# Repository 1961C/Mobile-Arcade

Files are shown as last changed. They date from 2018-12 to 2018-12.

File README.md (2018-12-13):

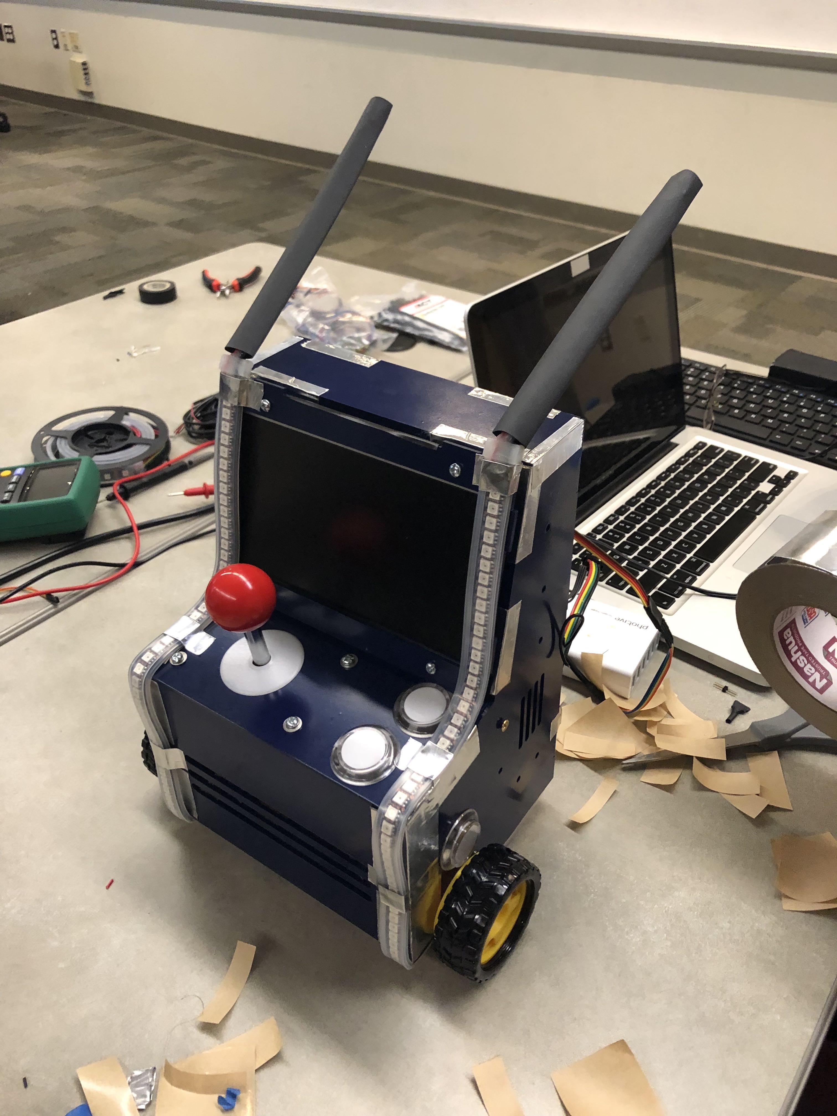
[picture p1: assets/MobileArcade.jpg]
Mobile Arcade


### Table of Contents
* [Concept](#concept)
* [System Design](#system-design)
  * [Physical Enclosure](#physical-enclosure)
  * [Arcade Emulator](#arcade-emulator)
  * [Low-level Control](#low-level-control)
    * [Drive System](#drive-system)
    * [Lighting](#lighting)
  * [Power](#power)
* [Instructions](#instructions)
* [Results](#results)
* [Improvements](#improvements)

## Concept

> "Develop a mobile arcade cabinet that can be controlled over Bluetooth to enable ultimate portability and usability, while maintaining retro charm."

The Mobile Arcade was designed to incorporate a retro gaming experience with a quirky mobile chassis. The original idea was centered around a table top arcade experience with additional entertainment features, including vibrant and responsive lighting. In order to better suit and entertain the target audience (children aged 9 through 14), mobility was incorporated as well. With this in mind, the following design requirements were set:
1. Fully functional, single player, arcade system (ability to play NES and Atari games)
2. Visually pleasing enclosure with a retro feel
3. Interactive lighting
4. Basic Bluetooth-controlled mobility

## System Design

The design of the mobile arcade was divided into distinct subsystems: the physical enclosure, the arcade emulator, the low-level drive system and lighting control. Each of these systems are outlined here.

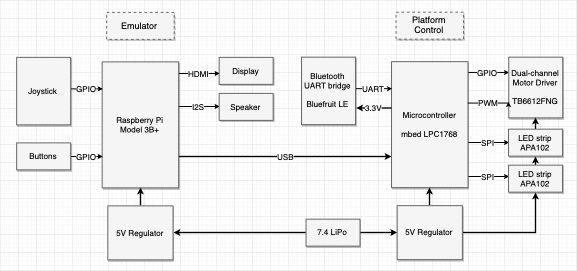
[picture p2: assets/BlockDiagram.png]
Block Diagram


* Raspberry Pi: Main processor
  * Handles arcade game emulator and UI
  * Interfaces with joystick and buttons
* Mbed LPC1768: Secondary processor
  * Handles lighting (LED strips)
  * Handles drive system (remotely commanded via the Bluetooth bridge)
* Dual-channel Motor Driver: Controls 2 motors in a tank-drive configuration
* Power: Li-Po battery and 5V regulator supply power to all components

### Physical Enclosure

The enclosure was designed using Dassault Systems’ Solid Works. Each portion of the seven component design was fitted together in software to ensure accurate dimensioning. The enclosure was then fabricated using 3/32" clear acrylic sheets and laser-cut at the Invention Studio.

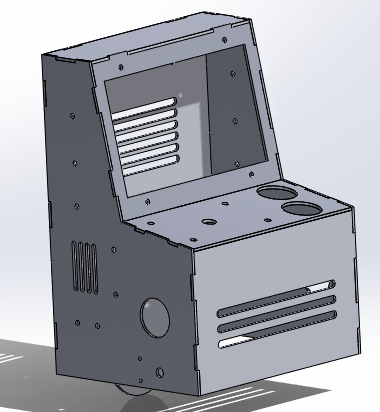
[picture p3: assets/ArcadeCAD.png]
CAD design


The overall shape of the enclosure resembles that of a standard arcade cabinet, with a few notable exceptions. The design is much simpler than standard cabinets, reducing the number of distinct components that need to be fabricated. Additionally, the cabinet incorporates mounting holes near the front specifically designed to accommodate geared drive motors. Along with the rear-mounted skid, this produces a "tank drive" configuration which allows the enclosure to maneuver deftly around its environment.

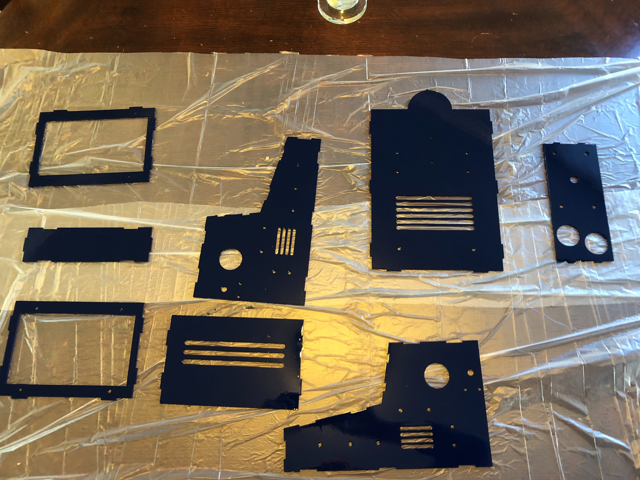
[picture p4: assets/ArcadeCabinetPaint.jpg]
Before cabinet assembly


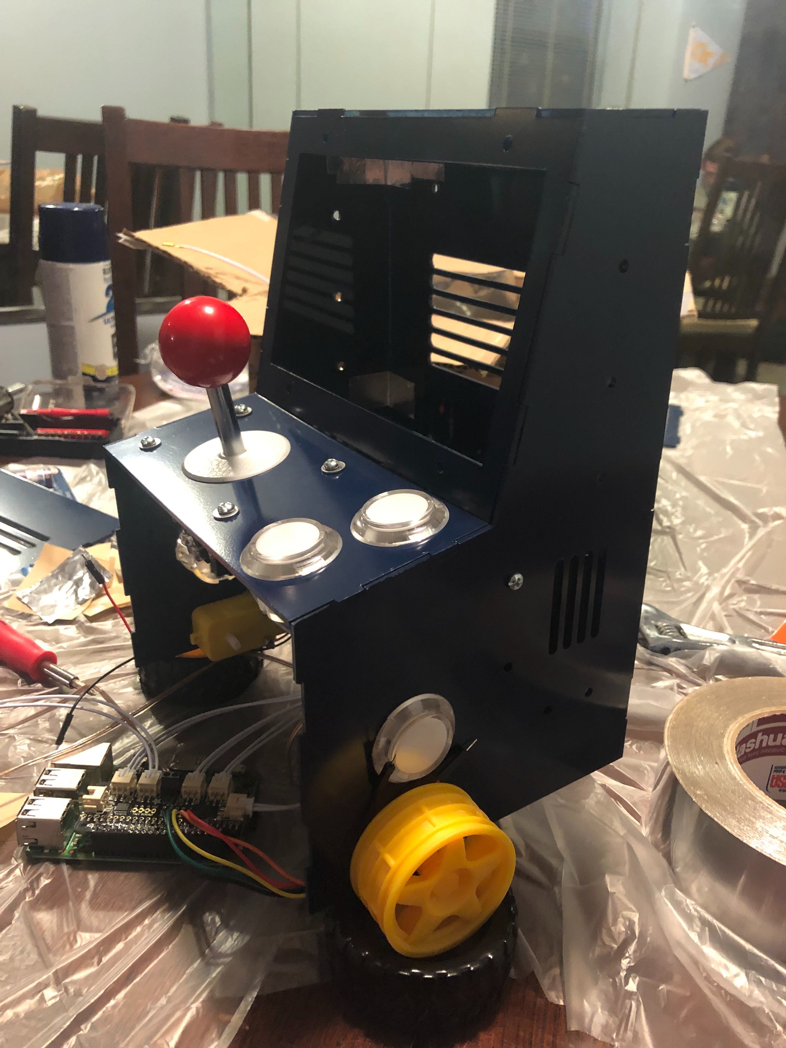
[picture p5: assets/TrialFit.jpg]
Trial fit

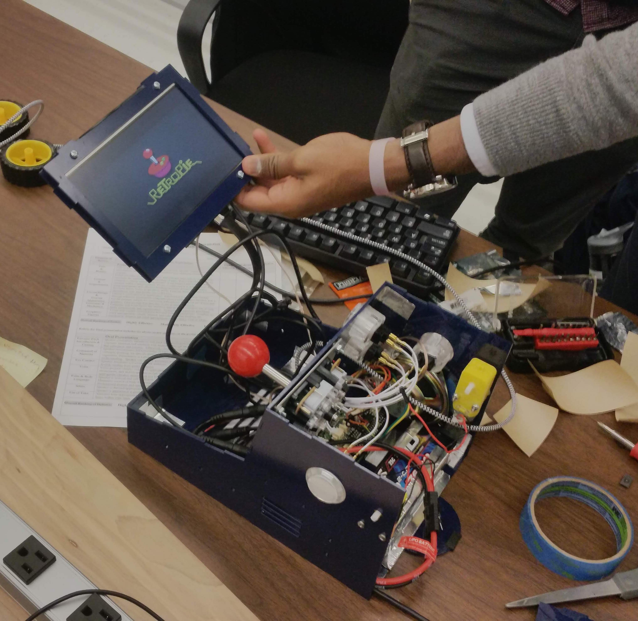
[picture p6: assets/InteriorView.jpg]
Interior view


Holes to fit the arcade controls (joystick and buttons) and LCD screen were included. Details about each of these is covered in the next section.

### Arcade Emulator

The emulation portion of the mobile arcade was split into two portions: the physical controls and the emulation software. The raspberry pi acts as the emulation computer for this project. A small LCD screen is used and is mounted above the joystick. This LCD uses hdmi to connect to the pi.

#### _Arcade Controls_

For controlling the arcade, a standard arcade joystick configuration with four additional buttons was chosen. The following parts were acquired from Adafruit to accomplish this:

* [Joystick](https://www.adafruit.com/product/480)
* [Button](https://www.adafruit.com/product/471)
* [Control Bonnet](https://www.adafruit.com/product/3422)
* [Connection Wires](https://www.adafruit.com/product/1949)
* [Speaker](https://www.adafruit.com/product/1314)

The joystick and buttons each have a specific location they fit into within the enclosure, and were chosen before the CAD model was finalized. The control bonnet connects directly to the GPIO header on the raspberry pi and allows each of the other elements to easily interface with the emulation software. 

Once each physical element is installed, [this guide](https://learn.adafruit.com/adafruit-arcade-bonnet-for-raspberry-pi) outlines the process of formally installing the Control Bonnet on the pi. In order for it to function correctly, specific software needs to be installed on the pi. This should be done after the emulation software is installed, as outlined below.

#### _Emulation Software_

The common emulation software [RetroPie](https://retropie.org.uk/) was chosen for this project. Retropie works seamlessly with the raspberry pi, the primary processor on the mobile arcade, and offers decent functionality. Installation is made fairly easy by the fact that the Retropie foundation provides a disk image for the raspberry pi. The steps that were followed for installing the software are as follows:

1. Download the Retropie disk image from their website
2. Burn the image to the raspberry pi's SD card
3. Boot the system and connect it to the ethernet using wifi or ethernet
4. Install the Control Bonnet software (Refer to previous section)
5. Follow the automatic key-bindings dialog
6. Copy ROM files to the appropriate location

Further details about this process (excluding the Control Bonnet) can be found on the [RetroPie](https://retropie.org.uk/) website.

### Low-level Control

The Mbed microcontroller was used to implement low-level lighting and drive system control. In order to neatly connect the Mbed to the Bluetooth bridge, motor driver, and the LED strips, a single-layer PCB was designed in Eagle and fabricated at the Mechanical Engineering electronics lab. 90º headers were used so that the connections occupied minimal vertical space.

The Eagle files for the PCB can be found [here](https://github.com/1961C/Mobile-Arcade/tree/master/eagle).

Mbed code can be found [here](https://os.mbed.com/users/abraha2d/code/MobileArcade/).

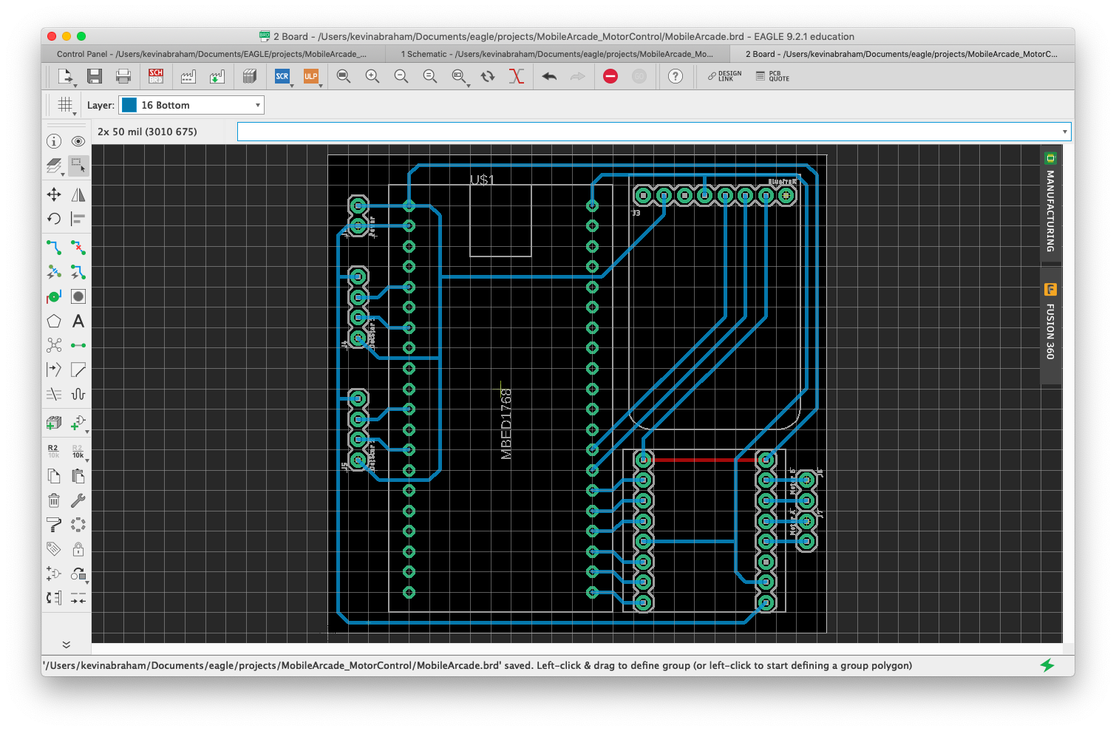
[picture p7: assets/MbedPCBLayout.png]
Mbed PCB design


#### Drive System

The drive system consists of two motors in a tank-drive configuration, with a rear skid for stability. Wheels were added to both sides of the motors (2 visible outside, 2 hidden inside). Not only does this improve stability and ensure traction, it also adds a level of redundancy to the drive system.

A custom Mbed library was used to control the motor driver. The basic library (located [here](https://os.mbed.com/users/simon/code/Motor/)) was extended to add a short brake feature. The extended motor driver library can be found [here](https://os.mbed.com/users/abraha2d/code/Motor/).

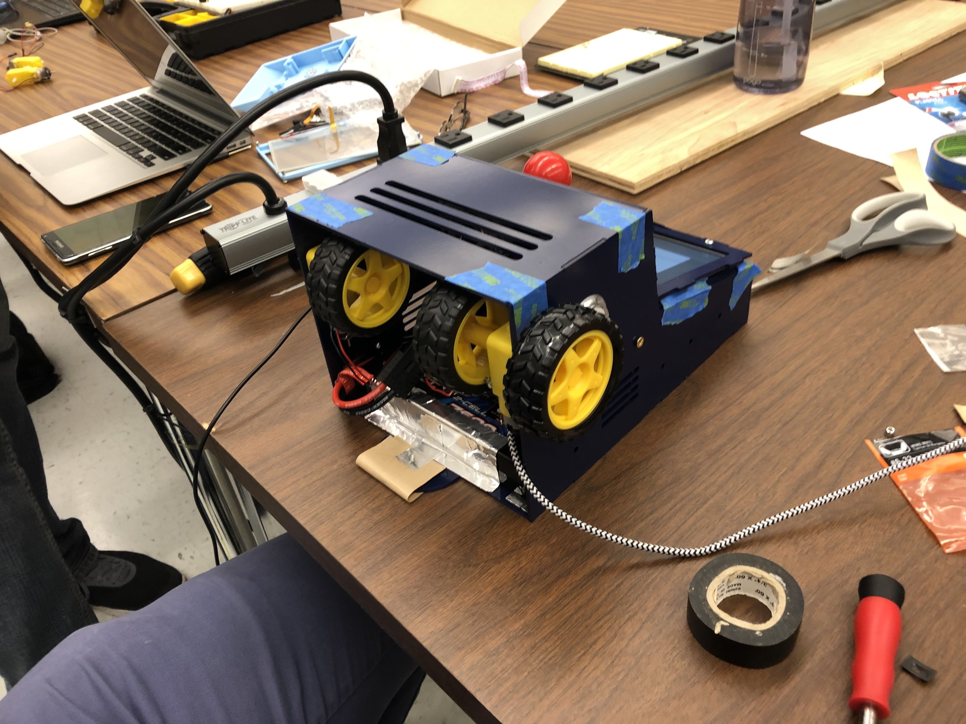
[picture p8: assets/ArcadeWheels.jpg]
Wheel setup


#### Lighting

[Dotstar LED strips](https://www.adafruit.com/product/2239) were used to implement the interactive lighting features of the Mobile Arcade. These were chosen over NeoPixels due to the standard SPI interface and relaxed timing requirements of the integrated APA102 chip, allowing for relatively easy interface with the Mbed. Since no official library was available for interfacing with the APA102, a simple library was created that fulfilled our needs (available [here](https://os.mbed.com/users/abraha2d/code/APA102/)).

The Mbed controls the LED strips in a way that simulates the actions of a real-world vehicle. Simulated lighting effects include headlights, foglights, blinkers, tail/brake lights, reverse lights, and underglow. These lighting effects are controlled in an appropriate way in relation to the movement of the enclosure.

The Mbed also accepts input from the Raspberry Pi over USB serial to synchronize lighting effects to certain events in the arcade emulator. For example, on emulation startup, a startup animation is shown on the LEDs. Other effects include a similar shutdown animation, as well as lighting theme changes when games are started/stopped.

### Power

The Mobile Arcade is powered using a wiring harness connected to a large lithium-ion battery pack. A 5V 3A regulator, connected the harness, is used to provide power for the Raspberry Pi, Mbed LPC1768, motors, and LED strips. The LCD is able to plug directly into the harness without further regulation. Fuses are integrated into the harness to protect sensitive components.

## Instructions

### Hardware setup

* Wiring harness
  * Battery power flows into a two way splitter
    * LCD Screen is powered off of one
    * 5V Regulator connects to the other
  * The 5V Regulator poweres the following items
    * Raspberry pi using a modified Micro USB Cable
    * MBed by powering its custom PCB Directly
    * Motors and LED scrips through the PCB
* Mbed PCB wiring
  * Connect 5V regulator output to power input
  * Connect DotStar LED strips to LED strip outputs
  * Connect motor leads to motor outputs
  * Insert Mbed, Bluetooth bridge, and motor driver in appropriate slots
  * Connect Mbed to Raspberry Pi with a USB cable
* Raspberry Pi Arcade Bonnet wiring ([Guide](https://learn.adafruit.com/adafruit-arcade-bonnet-for-raspberry-pi/connections))
  * Attach each button to one of the wire harness JST connector leads
  * Connect all buttons and the joystick to the Adafruit control bonnet
  * Using speaker wire, attach the speaker to the speaker header on the control bonnet

### Mbed setup

* Upload Mbed code (located [here](https://os.mbed.com/users/abraha2d/code/MobileArcade/))

### Raspberry Pi setup

* Follow RetroPie setup (located [here](retropie.org.uk))
  * Install Adafrit bonnet support software (located [here](https://learn.adafruit.com/adafruit-arcade-bonnet-for-raspberry-pi/software))
* Add runcommand scripts
  * Details about the runcommand scripts can be found [here](https://github.com/RetroPie/RetroPie-Setup/wiki/runcommand#runcommand-onstart-and-runcommand-onend-scripts)
  * Copy the files from '/runcommnads' in this repository to '/opt/retropie/configs/all/' on the raspberry pi
  * Plug the MBED into the pi using USB and ensure that the port (/dev/ttyXXXX) is correct in both runcommand files

## Results

[Demo](https://youtu.be/UGc3tqysLSs)

## Improvements

* Better connection between RPi and mBed
* Intgrate additional 5V regulator
* Add a caster to the back of the enclosure

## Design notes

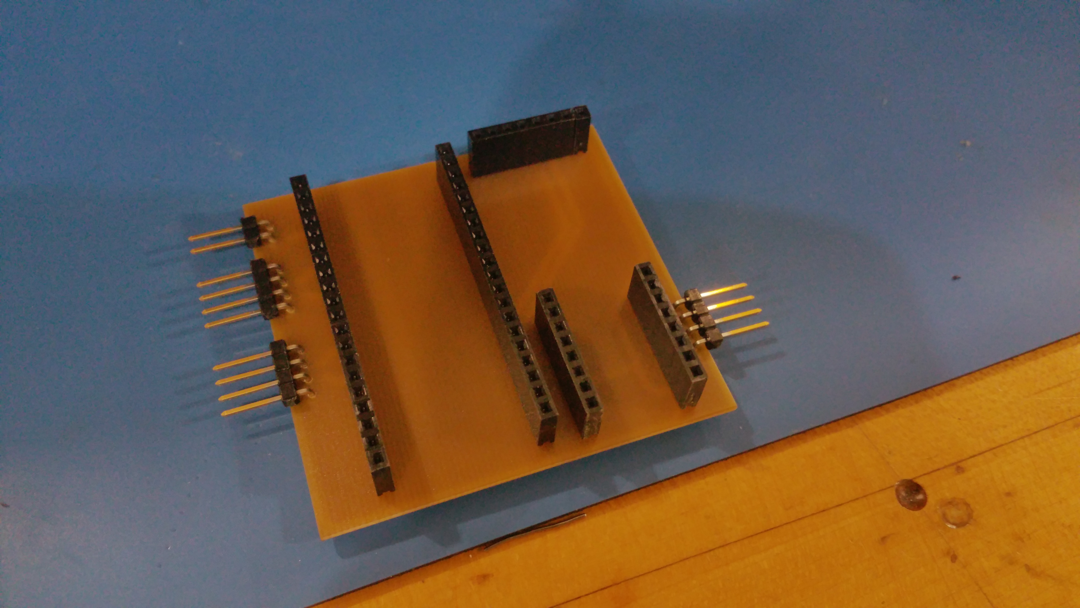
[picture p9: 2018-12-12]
assets/MbedPCB.jpg

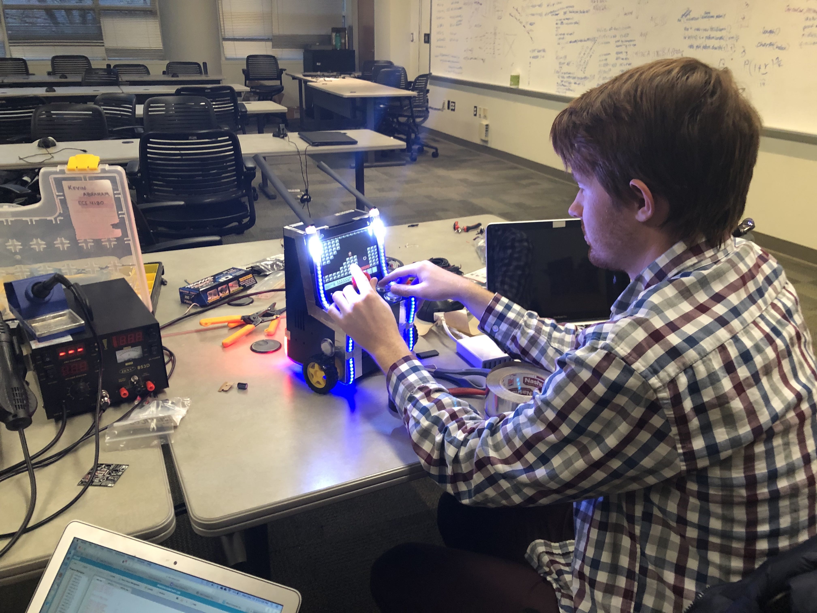
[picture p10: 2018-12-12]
assets/Demo.jpg

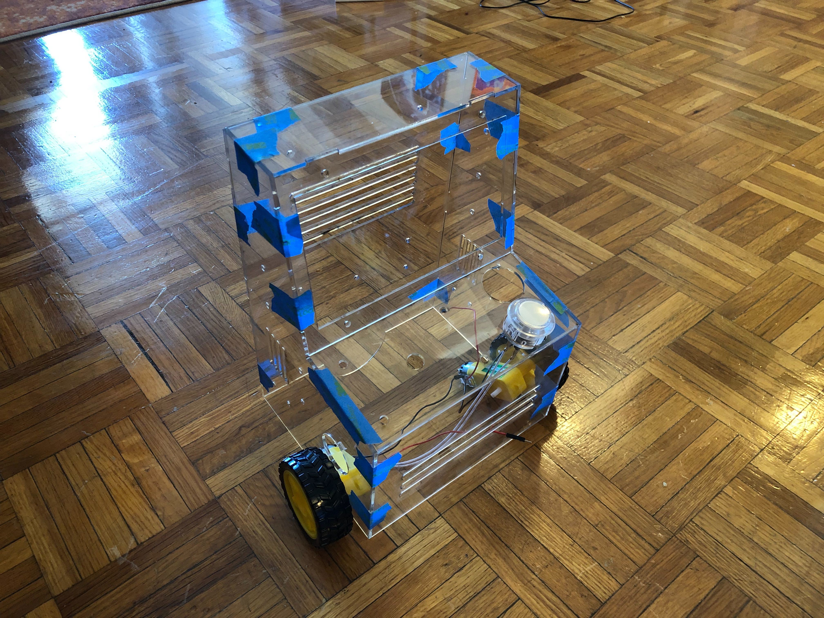
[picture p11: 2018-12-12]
assets/ArcadeCabinetAssym.jpg

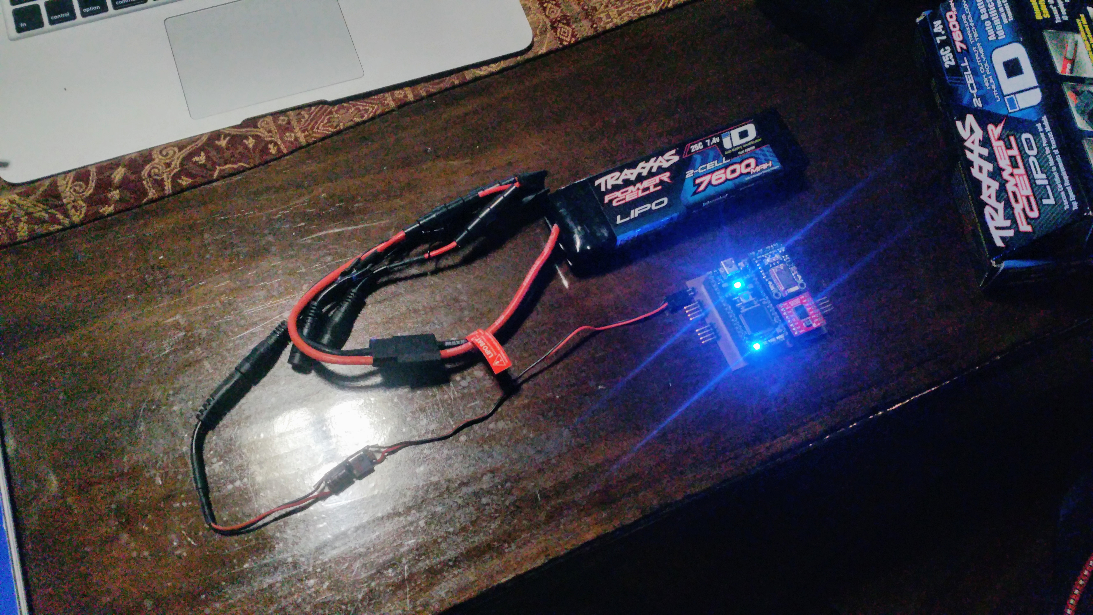
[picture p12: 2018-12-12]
assets/WireHarness.jpg

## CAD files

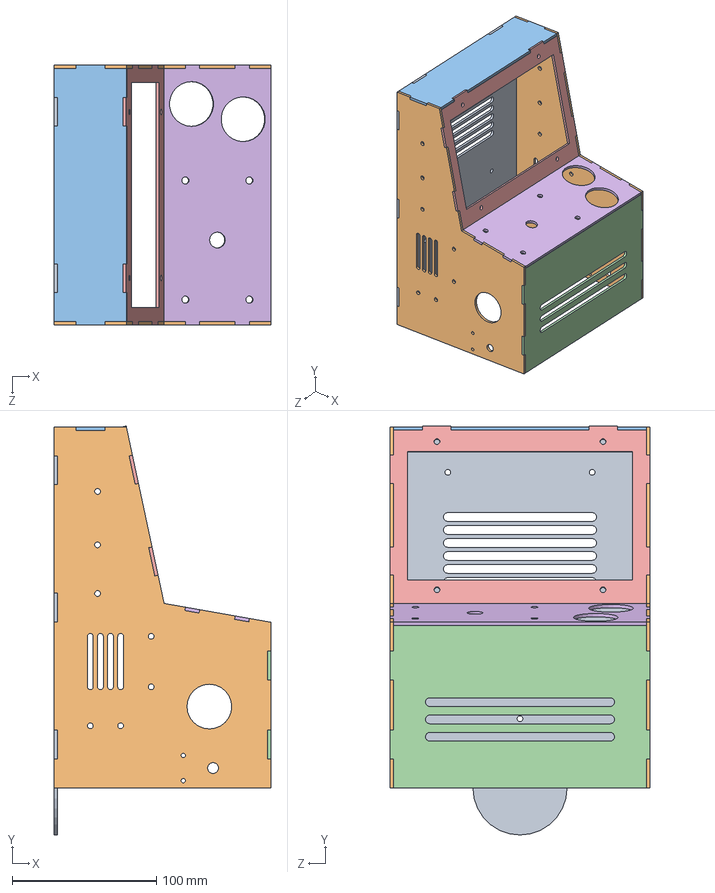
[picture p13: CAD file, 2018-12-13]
cad/solid-works/Assem1.SLDASM
150.0 x 283.3 x 180.0 mm
Backwall
Sidewall x 2
Top
Front
Screen
Panel

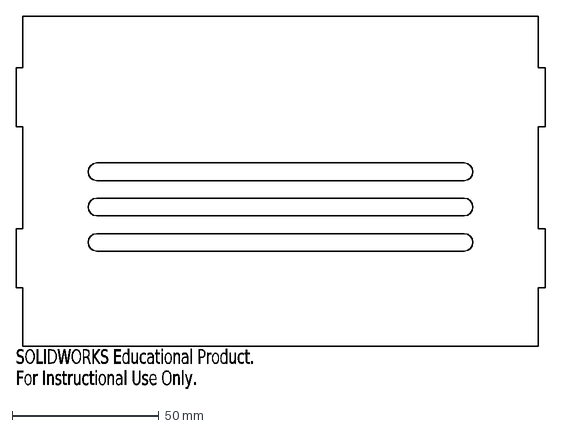
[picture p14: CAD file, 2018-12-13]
cad/Exports/Individual/1xFront.DXF
SOLIDWORKS Educational Product.
For Instructional Use Only.

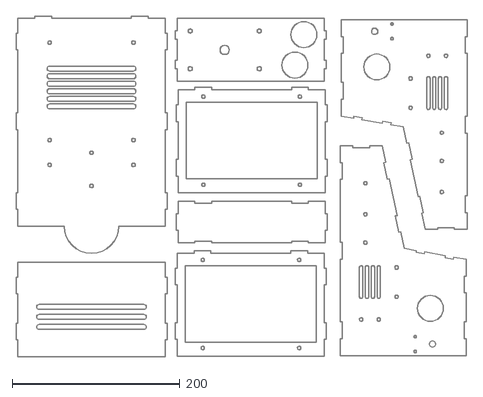
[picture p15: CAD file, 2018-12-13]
cad/Exports/Joined/Cutout_joined.dxf
537.5 x 405.7

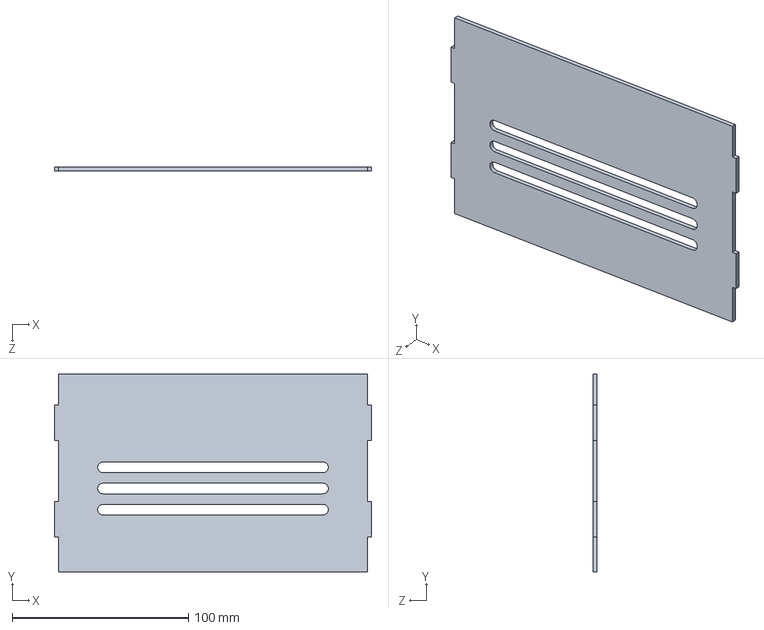
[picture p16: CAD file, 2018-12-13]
cad/solid-works/Front.SLDPRT
180.0 x 112.4 x 2.36 mm

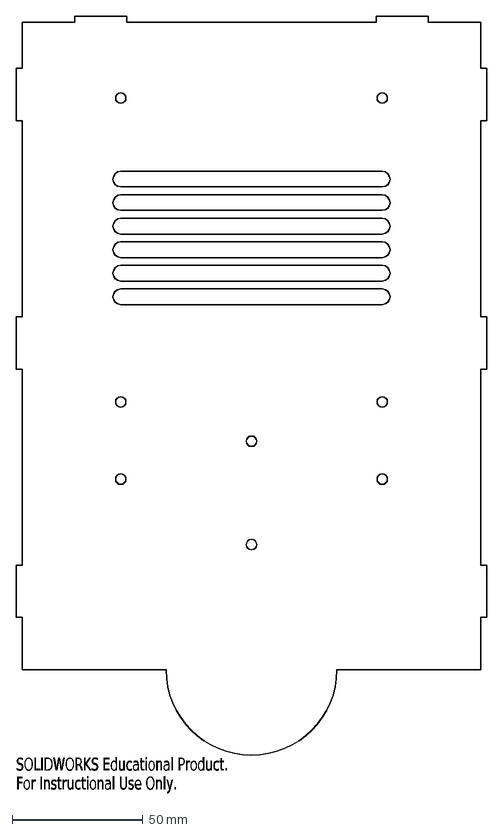
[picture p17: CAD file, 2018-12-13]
cad/Exports/Individual/1xBackwall.DXF
SOLIDWORKS Educational Product.
For Instructional Use Only.

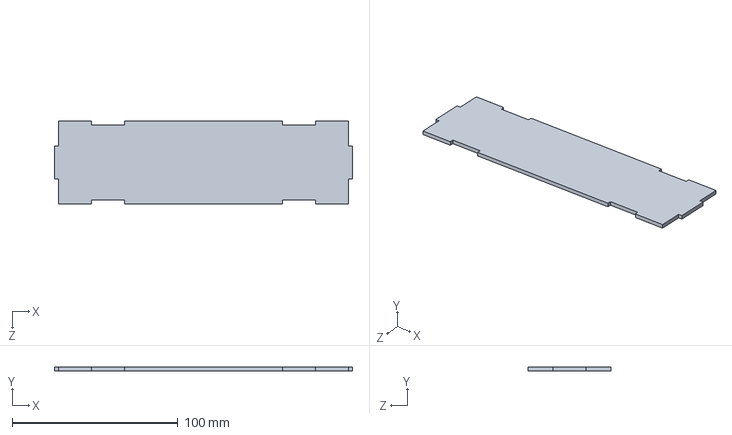
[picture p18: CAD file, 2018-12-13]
cad/solid-works/Top.SLDPRT
180.0 x 2.36 x 50.0 mm

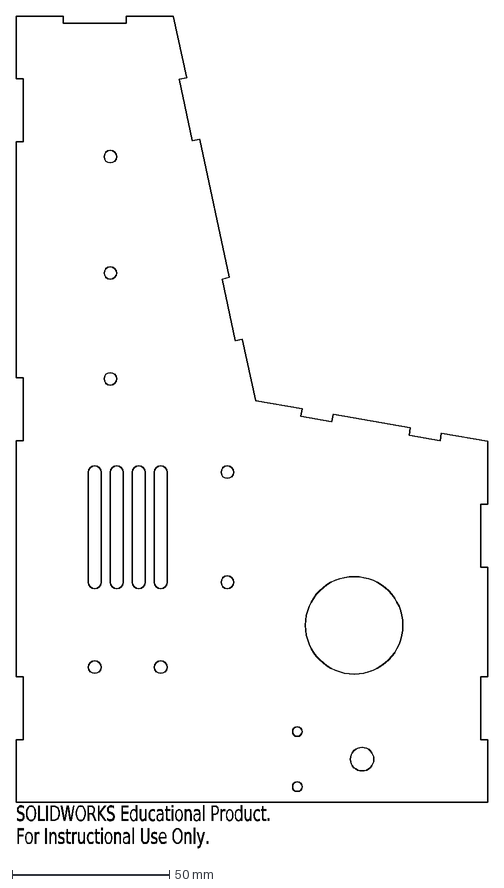
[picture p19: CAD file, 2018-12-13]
cad/Exports/Individual/2xSidewall.DXF
SOLIDWORKS Educational Product.
For Instructional Use Only.

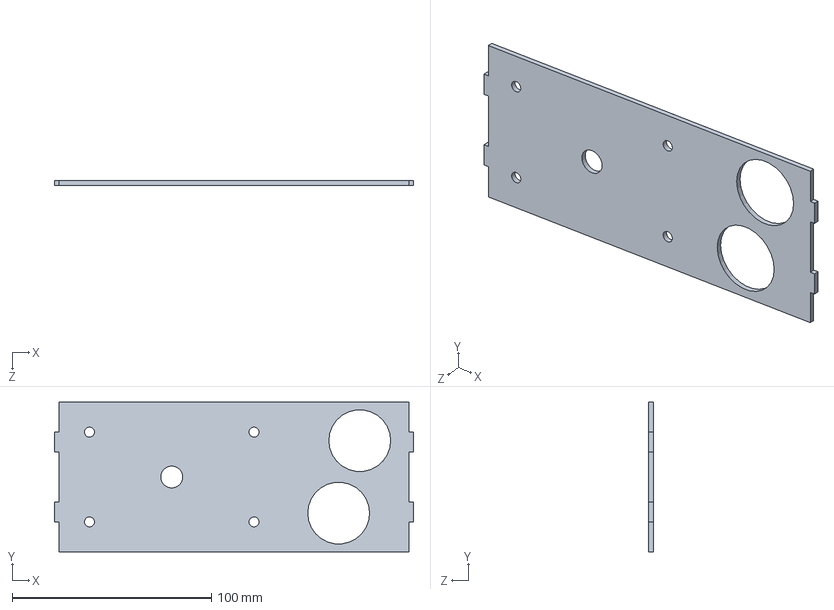
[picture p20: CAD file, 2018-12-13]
cad/solid-works/Panel.SLDPRT
180.0 x 75.0 x 2.36 mm

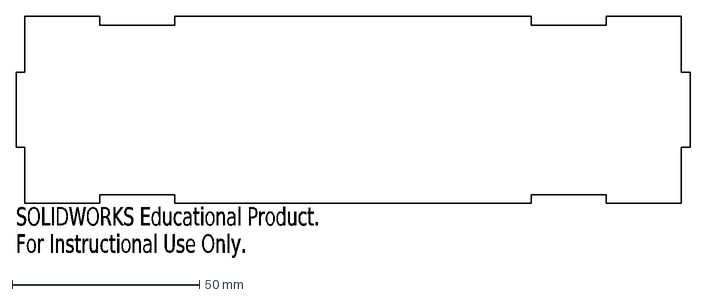
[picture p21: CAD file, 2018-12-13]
cad/Exports/Individual/1xTop.DXF
SOLIDWORKS Educational Product.
For Instructional Use Only.

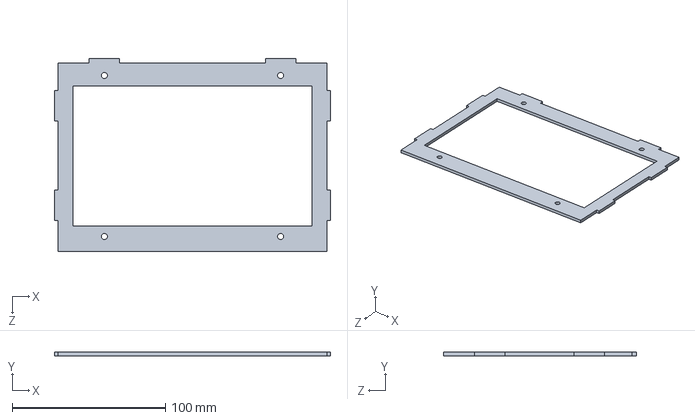
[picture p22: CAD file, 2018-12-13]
cad/solid-works/Screen.SLDPRT
180.0 x 2.36 x 125.7 mm

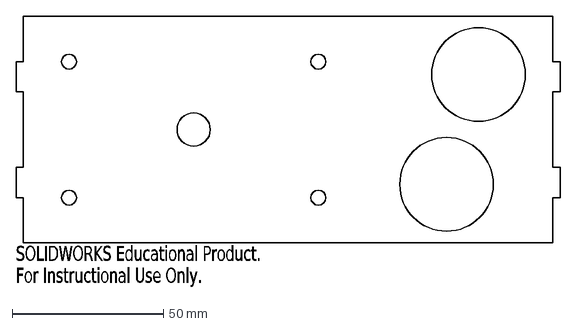
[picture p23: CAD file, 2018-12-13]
cad/Exports/Individual/1xPanel.DXF
SOLIDWORKS Educational Product.
For Instructional Use Only.

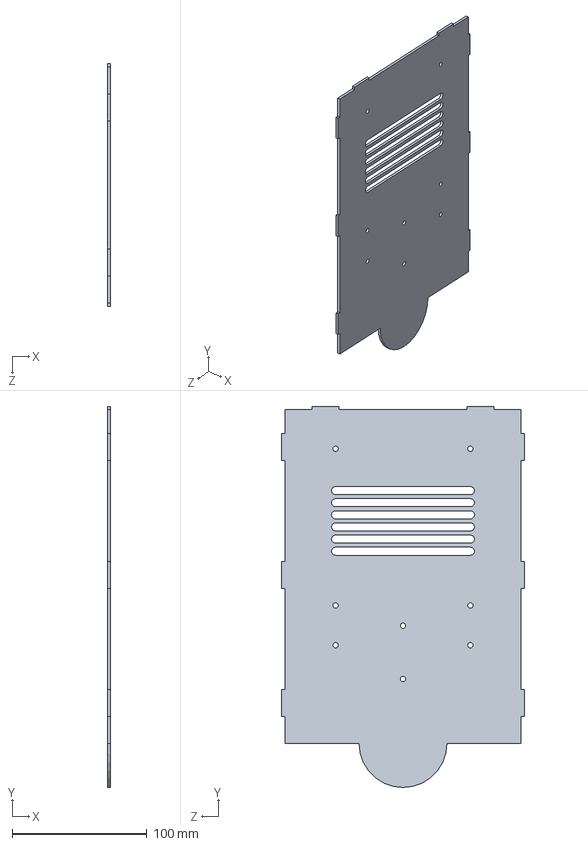
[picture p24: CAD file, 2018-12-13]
cad/solid-works/Backwall.SLDPRT
2.36 x 282.6 x 180.0 mm

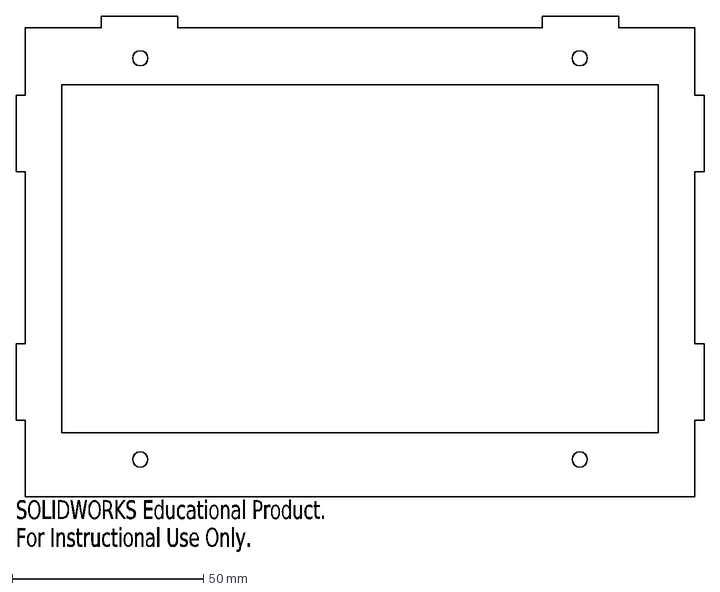
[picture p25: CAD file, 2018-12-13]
cad/Exports/Individual/1xScreen.DXF
SOLIDWORKS Educational Product.
For Instructional Use Only.

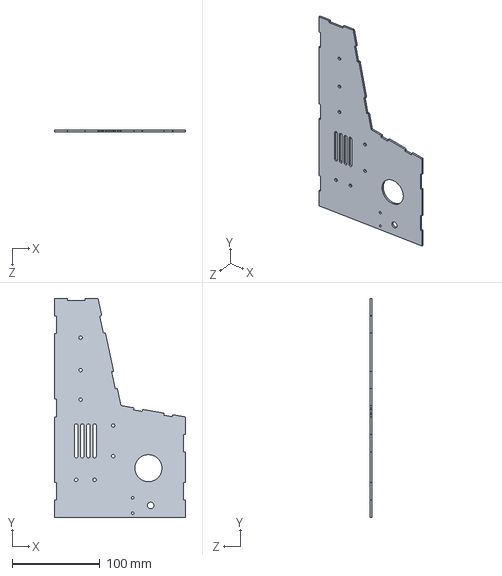
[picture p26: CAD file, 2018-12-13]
cad/solid-works/Sidewall.SLDPRT
150.0 x 250.0 x 2.36 mm

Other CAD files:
cad/Exports/Joined/Cutout_joined.dwg

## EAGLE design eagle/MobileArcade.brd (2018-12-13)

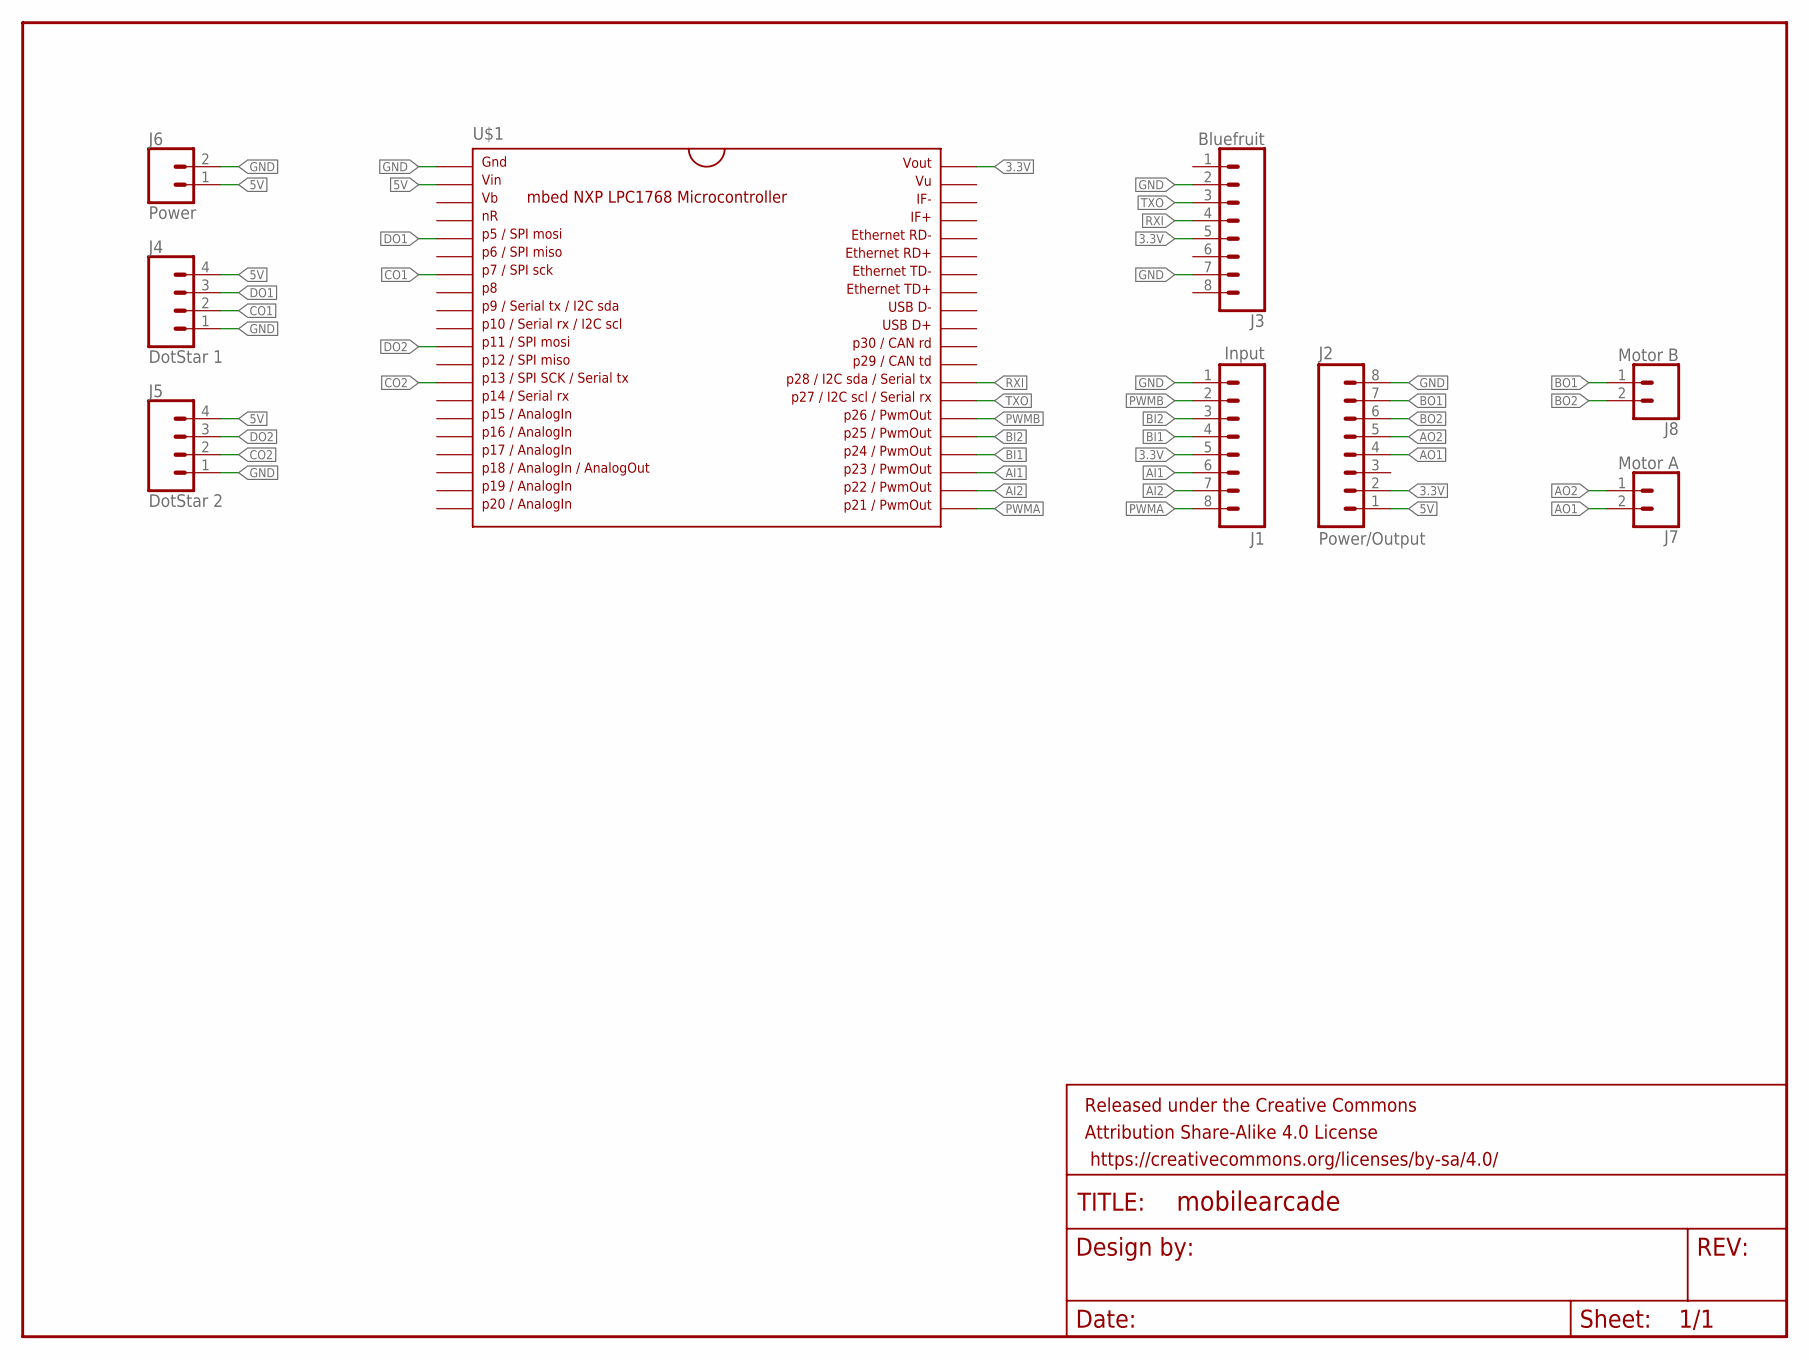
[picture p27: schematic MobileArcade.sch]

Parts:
FRAME1: FRAME-LETTERNO_PACKAGE; DUMMY
J1: Input; 1X08
J2: Power/Output; 1X08
J3: Bluefruit; 1X08
J4: DotStar 1; 1X04
J5: DotStar 2; 1X04
J6: Power; 1X02
J7: Motor A; 1X02
J8: Motor B; 1X02
U$1: MBED1768; DIL40_0.9

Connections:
3.3V: J1.5, J2.2, J3.5, U$1.40
5V: J2.1, J4.4, J5.4, J6.1, U$1.2
AI1: J1.6, U$1.23
AI2: J1.7, U$1.22
AO1: J2.4, J7.2
AO2: J2.5, J7.1
BI1: J1.4, U$1.24
BI2: J1.3, U$1.25
BO1: J2.7, J8.1
BO2: J2.6, J8.2
CO1: J4.2, U$1.7
CO2: J5.2, U$1.13
DO1: J4.3, U$1.5
DO2: J5.3, U$1.11
GND: J1.1, J2.8, J3.2, J3.7, J4.1, J5.1, J6.2, U$1.1
PWMA: J1.8, U$1.21
PWMB: J1.2, U$1.26
RXI: J3.4, U$1.28
TXO: J3.3, U$1.27

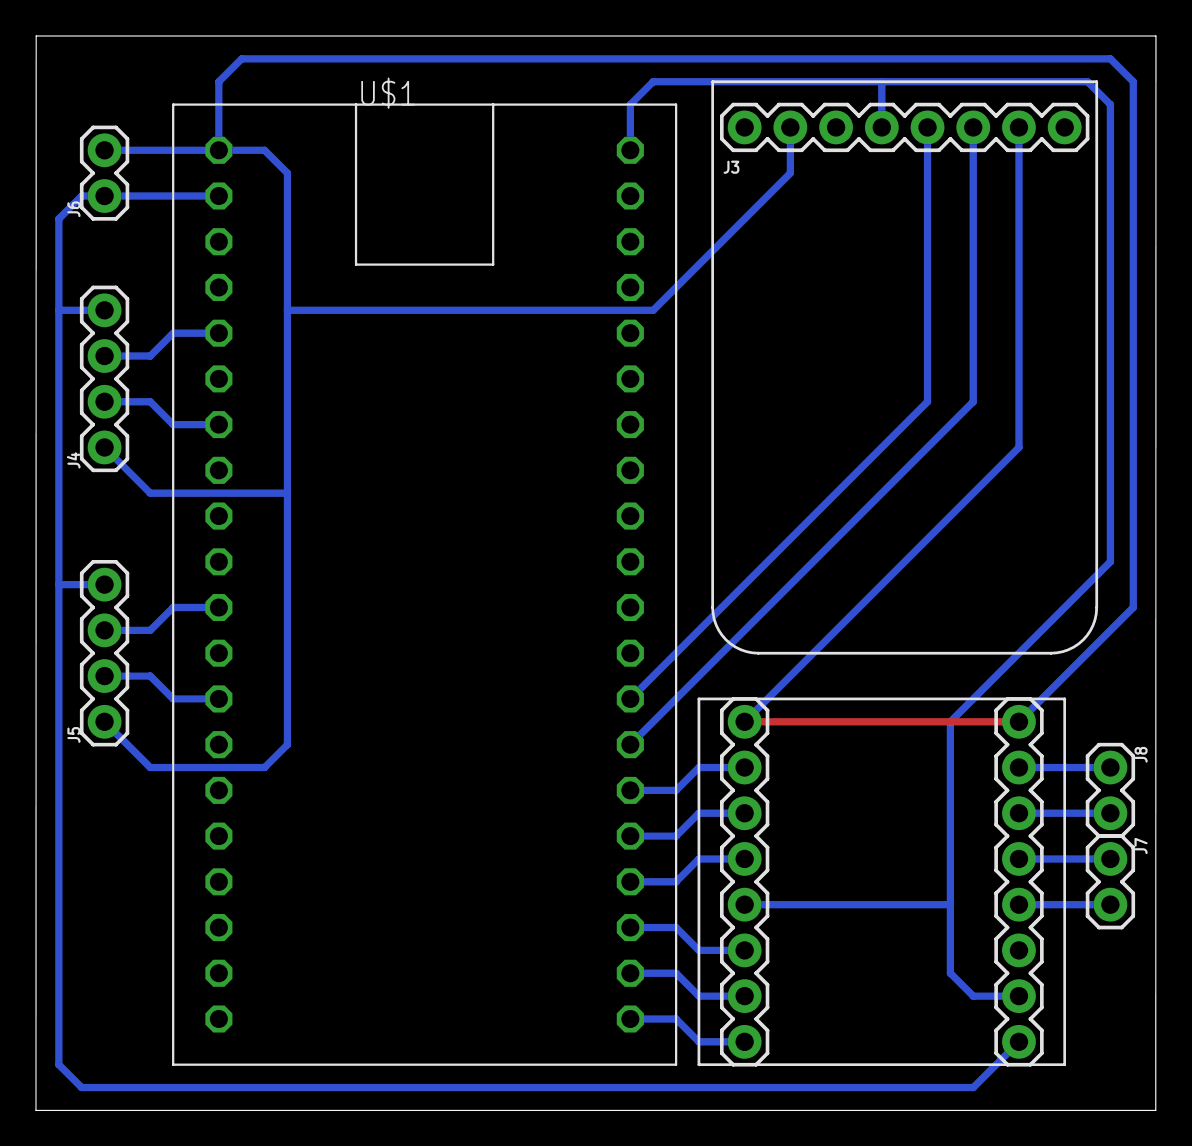
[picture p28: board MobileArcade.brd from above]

Board: 2 copper layers, 62.2 x 59.7 mm, 10 parts (0 on the bottom side), 19 nets.

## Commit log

2018-12-13 Add mbed pcb eagle files
    [MobileArcade.brd, MobileArcade.sch]
2018-12-13 Update physical enclosure section
2018-12-13 Wiring harness pic doesn't add much value. Poof.
2018-12-13 Basic wire harness and spell check
2018-12-13 Added cad and runcommands
    [1xBackwall.DXF, 1xFront.DXF, 1xPanel.DXF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]
2018-12-13 Made folder names consistant
    [Assem1.SLDASM, Backwall.SLDPRT, Front.SLDPRT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]

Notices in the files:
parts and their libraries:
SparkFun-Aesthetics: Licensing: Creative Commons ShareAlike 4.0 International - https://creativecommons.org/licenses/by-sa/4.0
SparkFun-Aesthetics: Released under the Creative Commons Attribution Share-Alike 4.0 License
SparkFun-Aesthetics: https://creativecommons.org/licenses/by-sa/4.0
